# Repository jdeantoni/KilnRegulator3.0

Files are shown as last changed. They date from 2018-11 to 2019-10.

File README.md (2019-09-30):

# KilnRegulator3.0
The objective is to provide a cheap and up to date kiln regulator based on a micro controller and a smart phone app
Please clone with ``git clone --recursive https://github.com/jdeantoni/KilnRegulator3.0.git``

## Website

https://jdeantoni.github.io/KilnRegulator3.0/

## Server readme

See `raspberrypi/`

## Client readme

See `mobile/`

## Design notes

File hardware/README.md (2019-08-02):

this folder contains the electronic level of the kiln regulator, i.e., breakboard, schematics, PCB, etc.
The development is made with Fritzing (https://fritzing.org/home/)

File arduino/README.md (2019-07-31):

# Prepare

Download and extract the Arduino IDE from
https://www.arduino.cc/en/Main/Software

Then set the environment variables according to the path of the extracted Arduino IDE (assuming it is in the current directory):
```
export ARDUINO_DIR="$(pwd)/arduino-1.8.7"
export PATH="${PATH}:${ARDUINO_DIR}"
```

Supported versions: 1.8.3 to 1.8.7 (included)

On ArchLinux, simply install the `arduino` package from the community repository.

# Build

```
git submodule update --init
make
```

# Deploy

```
make upload
```

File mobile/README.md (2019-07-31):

# KilnRegulator Client in React Native

## Dependencies

Install Expo, React Native and the project dependencies:

```
sudo npm install expo-cli --global
sudo npm install react-native-cli --global
npm install
```

## Build

Generate API client from Swagger:

```
./generate-client.sh
```

## Run

Launch the project on your terminal with Expo:

```
expo start
```

For the next steps, follow the instructions on your terminal and your browser at http://localhost:19002/.
If you want to use your own phone to test the app, download the [Expo app](https://expo.io) on your phone and scan the QR code from Expo.
Open it in the [Expo app](https://expo.io) on your phone to view it.

## Notes

In case of errors:
- If there is a connection error, please go to the webpage opened when you launched `expo start`, choose the *tunnel* mode and open it again in the expo app.
- For the emulation, check if `adb` is updated. If you have more than one installations of ADB, check the versions.
If you are using Genymotion, localize the Android SDK in the settings.
- Check if the ip address is correct. You may have to modify it each time you change your network.
With PowerShell:
```
$env:REACT_NATIVE_PACKAGER_HOSTNAME = “<IP>”
```
- If the terminal displays some errors, don't hesitate to reload Expo.
- If the QR code doesn't appear, reload Expo.
- If the bundle can't be constructed, add a dummy line in the code, the build may start.
- Check there is an unique instance of the app on your phone.

## Deploy

### Prepare

Make sure the `ANDROID_HOME` environment variable is set to the Android SDK path, eg. `~/Android/Sdk`:
```
export ANDROID_HOME="$HOME/Android/Sdk"
```

#### Eject

```
./eject.sh
```

#### Generate signing key

```
keytool -genkey -v -keystore android/app/my-release-key.keystore -alias my-key-alias -keyalg RSA -keysize 2048 -validity 10000 -storepass "password" -keypass "password" -dname "CN=Unknown, OU=Unknown, O=Unknown, L=Unknown, ST=Unknown, C=Unknown"
```

#### Add signing configuration

```
patch -p1 -i android-sign.patch
```

### Build & deploy

#### Generate signed apk

```
./android/gradlew -p android assembleRelease
```

#### Install signed apk

```
adb install ./android/app/build/outputs/apk/release/app-release.apk
```

## Screen navigation

### Home Page

When the app is launched, the home page display two buttons:
* You can connect your device to your kiln using the server IP address (don't forget the port).
* If you're not next to your kiln, there is an off line mode.

### Program choice

You can modify and create programs from this page. Select a program in the list, then, you have four options:
* Edit the program
* Duplicate the program
* Delete the program
* Launch the program

### Program edition

Edit the program in this page. You can edit the segments in the table and see results in the graph.
See in precision the temperature evolution with a cursor on the graph.

### Settings

Import and export kiln and phone programs.

### Tracking cooking

See the temperature evolution of the cooking. In brown, you can see the theoretical points, and in green the real ones.
When you connect your device with a kiln already heating, you will see first this screen.
When the kiln is stopped, you will see the last data from the cooking and the button will reinitialize the kiln state.
If an error appear, the icon in the header bar will change and you can access to the errors list.

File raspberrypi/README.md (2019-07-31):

# KilnRegulator Server on RaspberryPi

Arduino code will be automatically built and deployed on the Arduino when running through `docker-compose`.

## Dependencies (to be installed on the Raspberry or the development environment accordingly)
This README considers that the Raspbian OS is already installed on the Raspberry (see https://www.raspberrypi.org/downloads/raspbian/).

```
docker
docker-compose
```

## Prepare

To configure the Raspbian installation with a WiFi access point, watchdog, etc see conf/README.md

The arduino is connected through usb serial to the raspberry and the rasberry connected to the development computer (e.g., by using ethernet). Then, in the later, you can either connect to the raspberry through ssh or directly launch commands on the raspberry. But First, on the raspberry

Edit `raspberrypi/conf/udev/rules.d/arduino.rules` replacing the `idVendor` and `idProduct` by those of your Arduino device (that can be found in dmesg for instance).

```
sudo cp raspberrypi/conf/udev/rules.d/arduino.rules /etc/udev/rules.d
```

On Raspberry Pi:
```
git submodule update --init rpi3-mongodb3
```

## Build
From the root of the project,

```
docker-compose build
```

Or on Raspberry Pi:
```
docker-compose -f docker-compose-rpi.yml build
```

## Run

Arduino container is started before the server for it to deploy the code first then free the serial port for the server.

From the root of the project,

```
docker-compose up arduino && docker-compose up mongo server
```

Or on Raspberry Pi:
```
docker-compose -f docker-compose-rpi.yml up arduino && docker-compose -f docker-compose-rpi.yml up mongo server
```

## Notes

API can be viewed and tried at http://localhost:3000/docs

Bug with Linux 4.19 and Docker 18.09
https://github.com/docker/for-linux/issues/480

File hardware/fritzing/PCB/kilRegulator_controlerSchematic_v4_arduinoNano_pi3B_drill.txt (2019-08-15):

; NON-PLATED HOLES START AT T1
; THROUGH (PLATED) HOLES START AT T100
M48
INCH
T1C0.117717
T2C0.078740
T3C0.106299
T4C0.110236
T100C0.035000
T101C0.042000
T102C0.036000
T103C0.047244
T104C0.039370
T105C0.038000
T106C0.098425
T107C0.015748
%
T1
X024261Y001476
T2
X008839Y021483
X002934Y021483
X008761Y005676
X002961Y005676
T3
X024261Y020676
X001461Y020676
X024361Y008976
T4
X001461Y001376
T100
X011595Y015183
X016829Y020354
X015595Y015183
X021438Y015361
X019214Y014746
X016882Y015361
X021438Y020301
T101
X017894Y012821
X020874Y012821
T102
X002861Y019576
X002861Y010576
X002861Y008576
X008861Y017576
X008861Y020576
X008861Y009576
X002861Y011576
X008861Y019576
X008861Y016576
X008861Y018576
X002861Y006576
X008861Y010576
X008861Y007576
X002861Y009576
X002861Y013576
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

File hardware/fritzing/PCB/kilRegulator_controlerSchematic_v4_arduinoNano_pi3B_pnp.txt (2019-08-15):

*Pick And Place List
*Company=
*Author=
*eMail=
*
*Project=kilRegulator_controlerSchematic_v4_arduinoNano_pi3B
*Date=16:24:04
*CreatedBy=Fritzing 0.9.3b.04.19.5c895d327c44a3114e5fcc9d8260daf0cbb52806
*
*
*Coordinates in mm, always center of component
*Origin 0/0=Lower left corner of PCB
*Rotation in degree (0-360, math. pos.)
*
*No;Value;Package;X;Y;Rotation;Side;Name
1;;;24.4348;-29.4046;0;Bottom;Copper Fill4
2;;;29.0576;-29.5316;0;Bottom;Copper Fill5
3;;;38.4556;-34.4338;0;Bottom;Copper Fill30
4;;;28.2194;-7.0018;0;Bottom;Copper Fill14
5;;;53.37;-13.149;90;Bottom;Max31856
6;;;30.8864;-7.6368;0;Bottom;Copper Fill13
7;;;14.889;-34.4935;180;Bottom;arduino
8;;;33.4712;-15.5907;0;Bottom;Via1
9;;;8.2296;-20.5146;0;Bottom;Copper Fill10
10;;;40.8065;-14.6831;0;Bottom;Via5
11;;;40.8118;-5.77023;0;Bottom;Via4
12;;;40.7797;-6.3414;0;Bottom;Copper Fill36
13;;;58.2676;-21.048;0;Bottom;Copper Fill32
14;;SIP (Single Inline) [THT];22.0357;-3.28432;-90;Bottom;Screen (bottom side)
15;;;11.8237;-4.2332;0;Bottom;Copper Fill17
16;;;48.6446;-45.2714;180;Bottom;relay
17;;;33.2994;-8.3988;0;Bottom;Copper Fill12
18;;;15.8496;-27.8298;0;Bottom;Copper Fill3
19;;;44.2722;-28.7061;0;Bottom;Copper Fill41
20;;;40.7797;-5.3508;0;Bottom;Copper Fill37
21;;;7.523;-14.419;0;Bottom;Hole7
22;;;33.8074;-22.572;0;Bottom;Copper Fill34
23;;;30.7305;-49.3091;0;Bottom;TXT1
24;;;23.2918;-24.3881;0;Bottom;Copper Fill24
25;;;40.2844;-5.8461;0;Bottom;Copper Fill20
26;;;41.2496;-5.8461;0;Bottom;Copper Fill21
27;;;11.8237;-2.4552;0;Bottom;Copper Fill18
28;;;3.713;-52.519;0;Bottom;Hole14
29;;;32.2834;-28.1092;0;Bottom;Copper Fill1
30;;SOT-23 [SMD];43.017;-29.643;0;Top;Q3
31;;;44.2214;-18.2921;0;Bottom;Copper Fill27
32;;;17.3228;-29.557;0;Bottom;Copper Fill2
33;;;30.6422;-51.8527;0;Bottom;TXT1
34;;;3.713;-3.49698;0;Bottom;Hole13
35;;;8.2296;-23.0546;0;Bottom;Copper Fill9
36;;;26.8986;-34.4846;0;Bottom;Copper Fill8
37;;;40.7797;-5.3508;0;Bottom;Copper Fill19
38;;;32.4866;-23.8166;0;Bottom;Copper Fill33
39;;;40.259;-14.7361;0;Bottom;Copper Fill42
40;;;22.8346;-28.1092;0;Bottom;Copper Fill29
41;;;45.8978;-18.2921;0;Bottom;Copper Fill28
42;;;7.453;-54.567;0;Bottom;Hole5
43;;;61.625;-52.519;0;Bottom;Hole11
44;;;8.2296;-17.9746;0;Bottom;Copper Fill11
45;;;27.9146;-27.6266;0;Bottom;Copper Fill7
46;;;41.2496;-14.7361;0;Bottom;Copper Fill43
47;;;22.255;-14.419;0;Bottom;Hole8
48;;;41.2496;-14.7361;0;Bottom;Copper Fill26
49;;;61.625;-3.75098;0;Bottom;Hole10
50;;;6.4262;-19.3081;0;Bottom;Copper Fill22
51;;;41.2496;-5.8461;0;Bottom;Copper Fill38
52;;;14.3637;-4.2332;0;Bottom;Copper Fill15
53;;;32.4309;-54.3536;0;Bottom;TXT1
54;;screwterminal-3.5mm-2_lock;60.709;-47.0352;-90;Bottom;JP1
55;;;61.879;-22.801;0;Bottom;Hole9
56;;;22.453;-54.567;0;Bottom;Hole6
57;;;8.0518;-19.3081;0;Bottom;Copper Fill39
58;;;45.8978;-18.2921;0;Bottom;Copper Fill44
59;;;40.259;-14.7361;0;Bottom;Copper Fill25
60;220;THT;34.5331;-38.567;180;Bottom;R1
61;;;14.3637;-2.4552;0;Bottom;Copper Fill16
62;;300 mil [THT];49.2377;-32.567;180;Bottom;D1
63;;;23.2918;-24.3881;0;Bottom;Copper Fill40
64;;;48.9966;-12.3866;0;Bottom;Copper Fill35
65;;;21.6662;-24.3881;0;Bottom;Copper Fill23

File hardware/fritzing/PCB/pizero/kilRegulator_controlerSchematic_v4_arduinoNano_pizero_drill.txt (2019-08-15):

; NON-PLATED HOLES START AT T1
; THROUGH (PLATED) HOLES START AT T100
M48
INCH
T1C0.078740
T2C0.106299
T3C0.094488
T100C0.035000
T101C0.042000
T102C0.036000
T103C0.047244
T104C0.039370
T105C0.038000
T106C0.098425
T107C0.015748
%
T1
X008839Y021911
X008761Y006105
X002961Y006105
X002934Y021911
T2
X024587Y001833
X024587Y009313
T3
X024461Y011205
X001361Y001805
X001361Y011205
T100
X011595Y015612
X019214Y015174
X015595Y015612
X016882Y015790
X021438Y015790
X016829Y020783
X021438Y020730
T101
X020874Y013250
X017894Y013250
T102
X008861Y019005
X008861Y018005
X002861Y016005
X002861Y009005
X008861Y015005
X008861Y012005
X002861Y008005
X008861Y011005
X002861Y012005
X008861Y020005
X002861Y007005
X002861Y014005
X008861Y013005
X008861Y007005
X002861Y015005
X008861Y009005
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

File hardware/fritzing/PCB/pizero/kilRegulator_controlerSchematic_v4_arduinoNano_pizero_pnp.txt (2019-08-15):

*Pick And Place List
*Company=
*Author=
*eMail=
*
*Project=kilRegulator_controlerSchematic_v4_arduinoNano_pizero
*Date=16:39:52
*CreatedBy=Fritzing 0.9.3b.04.19.5c895d327c44a3114e5fcc9d8260daf0cbb52806
*
*
*Coordinates in mm, always center of component
*Origin 0/0=Lower left corner of PCB
*Rotation in degree (0-360, math. pos.)
*
*No;Value;Package;X;Y;Rotation;Side;Name
1;;;21.6408;-25.4766;0;Bottom;Copper Fill20
2;;;62.1329;-28.4615;0;Bottom;Hole11
3;;SOT-23 [SMD];42.403;-30.6555;0;Top;Q3
4;;;17.3482;-30.2645;0;Bottom;Copper Fill2
5;;;3.45891;-4.58549;0;Bottom;Hole13
6;;;33.4712;-16.6791;0;Bottom;Via1
7;;;48.6445;-46.3599;180;Bottom;relay
8;;;33.2994;-9.1063;0;Bottom;Copper Fill8
9;;;22.4528;-55.6555;0;Bottom;Hole6
10;;;44.45;-33.7062;0;Bottom;Copper Fill18
11;;;41.9862;-31.6742;0;Bottom;Copper Fill31
12;;;26.8986;-35.5731;0;Bottom;Copper Fill7
13;;;11.8237;-4.5597;0;Bottom;Copper Fill13
14;;;42.8117;-39.3323;0;Bottom;Copper Fill15
15;;;33.1891;-55.4421;0;Bottom;TXT1
16;;;29.928;-55.494;0;Bottom;TXT2
17;;;22.255;-15.5074;0;Bottom;Hole8
18;;;62.4528;-4.65562;0;Bottom;Hole10
19;;;14.3637;-2.7817;0;Bottom;Copper Fill12
20;;;28.2194;-7.7093;0;Bottom;Copper Fill10
21;;300 mil [THT];49.2376;-33.6555;180;Bottom;D1
22;;;62.4528;-23.6554;0;Bottom;Hole9
23;;;58.3184;-21.5777;0;Bottom;Copper Fill26
24;;;45.4025;-32.7791;0;Bottom;Copper Fill34
25;;SIP (Single Inline) [THT];22.0356;-3.61069;-90;Bottom;Screen (bottom side)
26;;;8.0518;-20.3966;0;Bottom;Copper Fill33
27;;;31.2922;-52.6523;0;Bottom;TXT1
28;;;23.2664;-25.4766;0;Bottom;Copper Fill21
29;;;46.3296;-33.7062;0;Bottom;Copper Fill35
30;;screwterminal-3.5mm-2_lock;60.963;-48.6317;-90;Bottom;JP1
31;;;29.0576;-30.6201;0;Bottom;Copper Fill4
32;;;24.4094;-30.4931;0;Bottom;Copper Fill3
33;;;32.3342;-28.6389;0;Bottom;Copper Fill1
34;;;32.766;-24.8543;0;Bottom;Copper Fill27
35;;;28.0839;-48.7986;0;Bottom;TXT2
36;220;THT;34.533;-39.6555;180;Bottom;R1
37;;;46.3296;-33.7062;0;Bottom;Copper Fill19
38;;;45.4025;-32.7791;0;Bottom;Copper Fill17
39;;;23.2664;-25.4766;0;Bottom;Copper Fill36
40;;;26.7462;-28.6389;0;Bottom;Copper Fill29
41;;;7.52301;-15.5074;0;Bottom;Hole7
42;;;34.1122;-23.5843;0;Bottom;Copper Fill28
43;;;31.8251;-52.2579;0;Bottom;TXT2
44;;;14.3637;-4.5597;0;Bottom;Copper Fill11
45;;;27.94;-28.7151;0;Bottom;Copper Fill6
46;;;35.0277;-49.6393;0;Bottom;TXT1
47;;;42.7228;-31.6742;0;Bottom;Copper Fill32
48;;;44.8564;-19.2282;0;Bottom;Copper Fill22
49;;;6.4262;-20.3966;0;Bottom;Copper Fill16
50;;;14.8889;-35.582;180;Bottom;arduino
51;;;11.8237;-2.7817;0;Bottom;Copper Fill14
52;;;15.6464;-2.3753;0;Bottom;Copper Fill30
53;;;54.0049;-14.1105;90;Bottom;Max31856
54;;;3.45891;-28.4615;0;Bottom;Hole12
55;;;7.45302;-55.6555;0;Bottom;Hole5
56;;;38.4302;-35.4715;0;Bottom;Copper Fill24
57;;;46.5328;-19.2282;0;Bottom;Copper Fill23
58;;;43.6372;-29.693;0;Bottom;Copper Fill37
59;;;30.8864;-8.3443;0;Bottom;Copper Fill9

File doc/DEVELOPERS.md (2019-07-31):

# Developer's manual

## Overall architecture

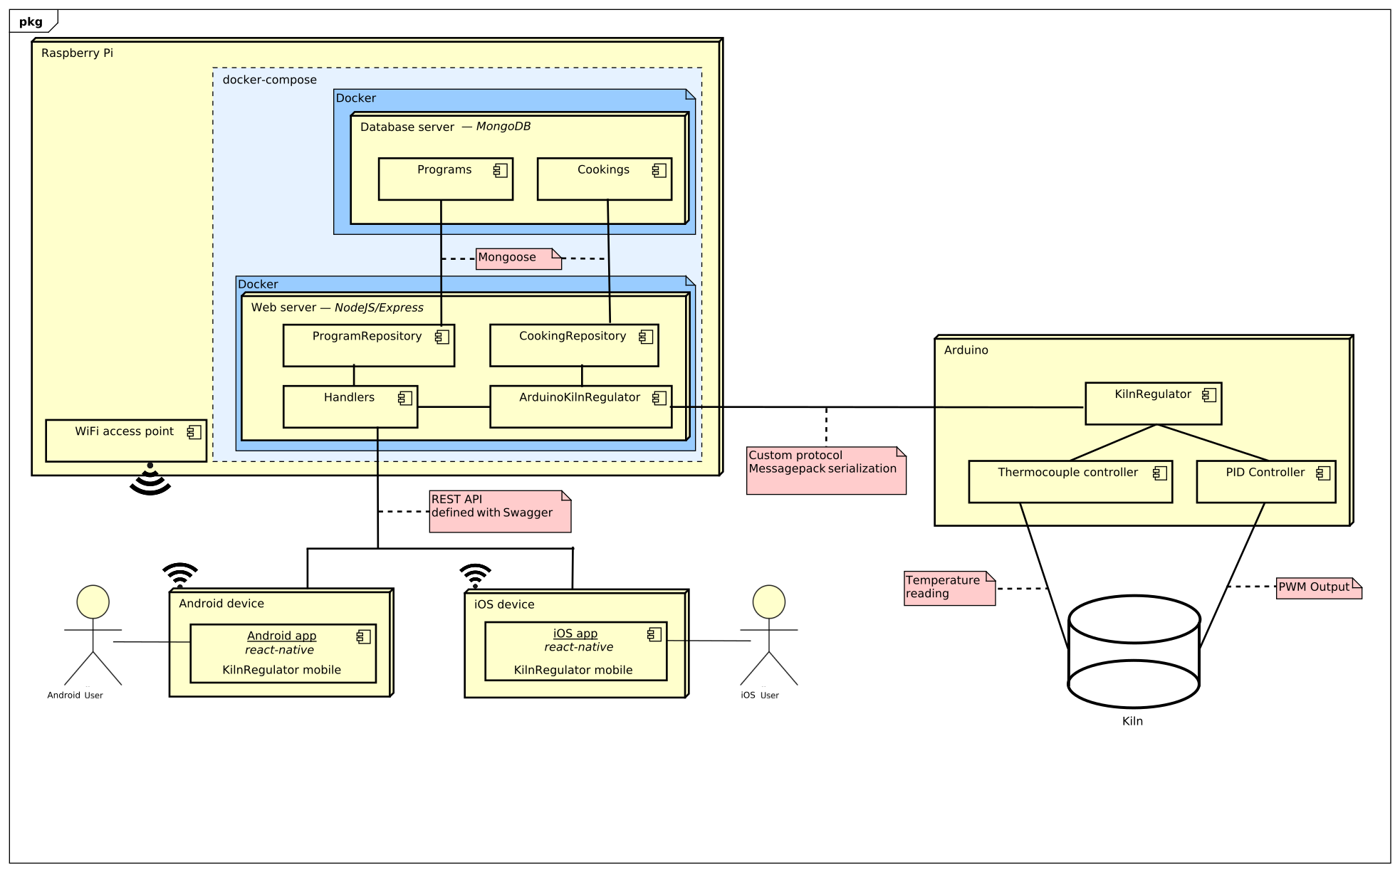
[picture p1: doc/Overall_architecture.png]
Croquis


### Communication protocol between Raspberry Pi Server and Arduino

Communication between the Raspberry Pi and Arduino is done through the virtual serial port exposed on top of the Arduino USB link.

Messages are serialized from JavaScript objects to Messagepack binary format.

Raspberry Pi Server sends command to the Arduino upon request coming from the client trough the REST API.

Commands sent to the Arduino are:
 * `["start", segmentCount]`: start the program transmitted through `segment` commands, switching from "ready" to "running" state
 * `["stop"]`: stop the current program before it has ended, forcing a switch from "running" to "stopped" state
 * `["reset"]`: reset to initial state, switching from "stopped" to "ready" state
 * `["segment", segmentNumber, targetTemperature, slope, duration]`: transmit a segment for the next program to run
 * `["timesync", timestamp]`: send current timestamp (in seconds) to synchronize Arduino's clock
 * `["setpoint", setpoint]`: manually set the target temperature

Arduino regularly sends status update:
```
{
	"command": "status",
	"s": kilnState,
	"eS": elementState,
	"cS": currentSegment,
	"t": temperature,
	"o": output,
	"sP": setPoint,
	"ts": timestamp
}
```
and timesync requests:
```
{
	"command": "timesync"
}
```

Message from the Raspberry Pi Server to the Arduino are always acknowledged by the Arduino. The Arduino compute a CRC8 of the received data and append it to the acknowledgment. Message contains a sequence ID that is sent back in the acknowledgment.

### Raspberry Pi Server REST API for Mobile client

REST API between the Raspberry Pi NodeJS server and the mobile React-Native app is defined using Swagger in the `doc/swagger.yaml` file.

After spinning up the Raspberry Pi NodeJS server (see below), the API documentation can be seen at <http://localhost:3000/docs>. API can be queried from inside the Swagger user interface, or by using the web browser or a command line utility such as `curl` for testing purposes.

The Raspberry Pi NodeJS server parses the Swagger file at runtime to handle routing.

The client libraries must be generated again from a Swagger editor or the command line Swagger generator after modifying the API description.

## Arduino

### Development environment

Arduino development requires installing the Arduino IDE locally. See `arduino/README.md`.
Although it may possibly be working on other platforms, the build system was used only on Linux so far.

#### Development

Please do not use the Arduino IDE itself but rather a standard text editor with EditorConfig support or an IDE with EditorConfig support as well.

#### Build & run

Connect the Arduino on a USB port and use the provided Makefile build system inside the `arduino` folder. Make sure the current user can write to the virtual serial port, check your distribution documentation if needed.

```
cd arduino
make upload
```

### Code style

Defined in `arduino/.editorconfig`
 * Single tab for indendation
 * LF line ending

### Code architecture

All the libraries are added as git submodules under the `src/` folder. Only the `src/kilnregulator/` subfolder actually contains original source code for the Arduino application.

## Raspberry Pi server

### Development environment

Raspberry Pi server development can be done both on a Raspberry Pi 3 or a standard computer with a Linux distribution, although keep in mind that the architecture is different. Raspberry Pi 3 is ARMv7-A (armhf on Debian), a PC is x86_64 (amd64 on Debian, note that i686 is not supported).

Raspberry Pi development requires `nodejs >= 8` and `npm` locally. Make sure you use a recent `npm` version or else modules may fail installing (repository server may throw 405 errors). You may encounter this issue with the latest `npm` package on Raspbian.

#### Development

Use the text editor or IDE of your choice, preferably with EditorConfig support or set the code style parameters manually.

#### Build & run

When running for the first time, start the MongoDB database inside Docker.
```
docker-compose up mongodb
```
Or on Raspberry Pi:
```
docker-compose -f docker-compose-rpi.yml up mongodb
```

Then connect the Arduino (deploy the Arduino code if needed, see above) and start the server:
```
cd raspberrypi
npm start
```

### Code style

Defined in the top-level `.editorconfig`
 * Two spaces for indendation
 * LF line ending

### Code architecture

#### `handlers/`

Request handlers, called by Swagger from the routes defined in the Swagger file. The name of the file must match the `operationId` of the route. A handler must always send something to the client, even an empty string if nothing needs to be sent. Most of the business logic is offloaded to modules inside `services/`

Please read Swagger documentation for details on the purpose of the handlers.

#### `services/`

Business logic for Arduino communication and database objects management.

 * `arduino.js`: encapsulate the Arduino serial port management
 * `arduinomessagepack.js`: manages the Arduino communication protocol: messagepack serialization/deserialization, output buffer, acknowledgments, timeout
 * `arduinokilnregulator.js`: operations on the Arduino as a KilnRegulator module such as handling a state update and stopping/starting a cooking
 * `arduinorepository.js`: Detects and maintain a list of available Arduino (as ArduinoKilnRegulator objects)
 * `cookingrepository.js`: some CRUD operations to manage cookings in database
 * `programrepository.js`: some CRUD operations to manage programs in database
 * `errorhandler.js`: error loggers with 4 severity levels, from warnings, recoverable errors to fatal errors and panic

#### `model/`

Database object models, state machine enums are also declared here, matching the enums declared in Arduino code. Objet models try to match the ones used for the REST API, declared in the Swagger file.

 * `kilnState.js`, `elementState.js`: state machine enums matching Arduino enums, not related to database
 * `db.js`: database connection handler
 * `model.js`: list of database object models
 * `cooking.js`, `program.js`: some object models to store cookings and programs in database

## Mobile app

### Development environment

#### Development

For React Native development, there is no specific IDE to work with, but you can use WebStorm, Visual Studio Code, Atom (with the plugin Nuclide) or your favorite JS text editor.
But you need to have installed on your computer: `npm`, `expo-cli` and `react-native-cli` (npm packages). For more information, see `mobile/README.md`.

#### Build & run

Connect your Android phone or your iPhone on the same network as your computer. Launch the Expo CLI. With the Expo app on your phone, scan the QR code on Expo CLI. Every modification in the code will reload the app on your phone.
```
cd mobile
expo start
```
When the app is opened, connect the mobile to the Raspberry Pi using its IP address (like: 123.1.1.1:3000). Don't forget the port.

### Code style

Defined in `.editorconfig` and modified in `mobile/.editorconfig`
 * Four spaces for indendation
 * LF line ending

### Code architecture

#### At root
 * `app.js`: program entry point (initialize the navigation tool and Redux).
 * `package.json`: list of dependencies.

#### `components/`
Contains all graphic components (table, charts, list items...). This components are reusable in several screens.

#### `screens/`
Represents project pages. Contains the main logic.

#### `navigation/`
Defines the stack navigation. All the screens must be declared here.

#### `helpers/`
Toolbox which contains useful functions. Mainly:
 * `ImageLoader.js`: Registers pictures and icons contained in the `assets/` directory.
 * `NavigationHelper.js`: Helps to edit the header bar.
 * `UnitsHelper.js`: Manages all units conversions (temperature, slope, time...).

#### `network/`
Used to call KilnRegulator3.0 API.
 * `APIClient.js`: Defines the differents client objects for each Swagger tag.
 * `NetworkRoutes`: Memorizes the server IP address.
 * `jsclient/`: Code generated by Swagger to call the API. Don't forget to generate it with the `mobile/generate-client.sh` script.

#### `store/`
Redux files needed to save programs with segments in a global local state. Use actions defined in `helpers/Constants.js` to alter the programs.

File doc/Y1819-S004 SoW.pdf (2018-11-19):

CASAGRANDE Guillaume, NOVAC Pierre-Emmanuel

# KilnRegulator3.0 (Y1819-S004)

## Introduction

Ce projet a pour but d’aider les céramistes dans le processus de cuisson. Notre rôle sera de proposer un système capable de contrôler une cuisson en se greffant aux fours de potiers. Ce genre de système existe déjà mais coûte plusieurs centaines voire milliers d’euros selon les modèles. Proposer un produit bien moins cher est donc l’une de nos priorités.

Les systèmes déjà existants sont fiables mais proposent peu de fonctionnalités. Les possibilités de personnalisation de cuisson étant réduites, nous souhaitons les élargir en proposant une application mobile permettant de créer et de modifier des programmes de cuisson précis. Cette application aura aussi pour but de suivre l’évolution des cuissons au cours du temps.

Cependant, pour convaincre les céramistes, il faudra proposer un système facile à prendre en main ressemblant aux produits qu’ils ont l’habitude de manipuler. Finalement, notre problématique est d’arriver à concevoir un système simple contrôlant une cuisson de poterie, moins coûteux que les produits existants sur le marché et proposant de nouvelles fonctionnalités facilitant le travail des céramistes.

## Description de la solution

Pour répondre à la problématique développée précédemment, nous proposerons deux modules qui communiqueront ensemble : une application mobile et un système embarqué (voir Fig. 1).

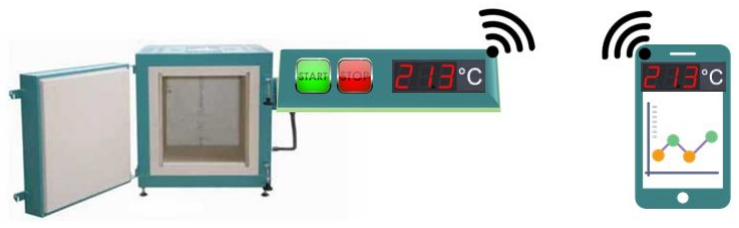
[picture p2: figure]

Figure 1 : Schéma représentatif des éléments majeurs intervenant dans le projet

Personas :
- Ludovic, 36 ans, est potier depuis que son père lui a légué son atelier. En plus de son lieu de travail, son père lui a laissé son savoir faire et une extrême minutie pour son travail. Ludovic aime donc contrôler avec précision le processus de création de ses œuvres. Il utilise un nouveau four qui lui a coûté cher, mais qui lui permet d’obtenir une fiabilité très élevée. Fan de technologie, il aimerait utiliser son téléphone pour contrôler son four, tout en gardant la fiabilité qu’il estime plus que nécessaire. Il souhaite aussi que le système agisse automatiquement ou au moins l’avertisse lors d’une anomalie (par exemple, lors d’une coupure de courant).
- Amélie, 56 ans, céramiste depuis son plus jeune âge, maîtrise largement son domaine. Son atelier fonctionne très bien, surtout grâce aux prix qui battent la concurrence. En fait, Amélie fait ce travail par passion et l’argent ne l’intéresse pas plus que ça. Par contre, son matériel coûte très cher, et elle n’ose pas le remplacer de peur qu’elle soit obligée d’augmenter ses prix. Elle aurait donc besoin d’un système de gestion de cuisson pas cher, voire même réutilisable pour ses différents fours.
- Albert, 44 ans, est un artisan touche-à-tout. Il travaille avec une petite équipe pour fabriquer de nombreux types d’objets en manipulant plusieurs matériaux. Il vend ses œuvres aux marché de sa ville ou à des particuliers sur Internet. Albert est expérimenté dans la céramique, mais cela lui arrive de faire des erreurs. Il oublie souvent qu’il a lancé une cuisson, et ne vérifie pas assez son état. Il aimerait donc un outil afin de suivre l’évolution de sa cuisson quand il est occupé ailleurs.

## Application mobile

### Scénarios d’usage

Scénario 1 :
1) Lancer l’application
2) Connecter l’application au four
3) Choisir le programme numéro 3 correspondant à la porcelaine
4) Démarrer la cuisson
5) Après 3 heures de cuisson, vérifier la température actuelle du four
6) Être alerté de la fin de cuisson

Scénario 2 :
1) Lancer l’application
2) Connecter l’application au four
3) Créer un nouveau programme
4) Identifier les segments du programme
5) Enregistrer le programme
6) Démarrer le programme créé
7) Après 2 heures de cuisson, être alerté qu’un problème est survenu
8) Stopper la cuisson
9) Consulter l’évolution de la température pour identifier le problème

Scénario 3 :
1) Réaliser une cuisson avec de la faïence
2) Trois semaines plus tard, consulter l’historique des cuissons passées
3) Identifier la cuisson de la faïence réalisée précédemment
4) Mémoriser le programme utilisé
5) Modifier le programme en augmentant la température d’un segment de 10°C
6) Démarrer une cuisson avec le nouveau programme

### Maquettes

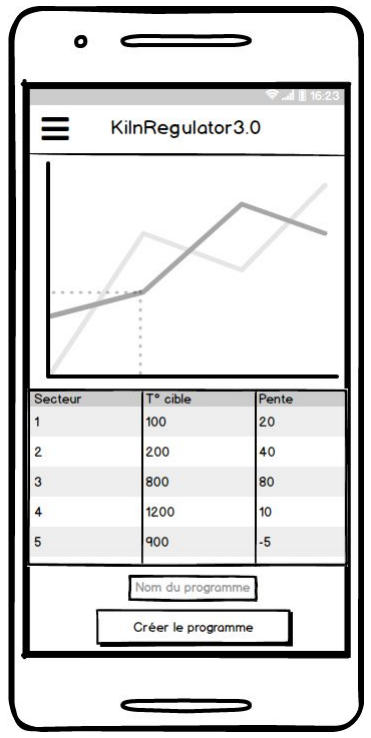
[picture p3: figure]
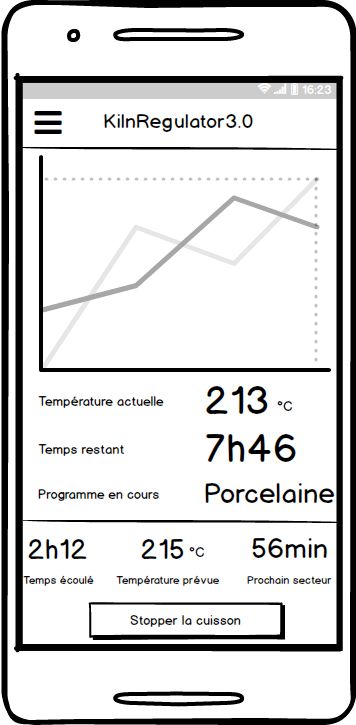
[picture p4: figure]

Figures 2 & 3 : Maquettes du suivi de la cuisson et de la création d’un programme

## Plateforme embarquée

L’application mobile agit sur une plateforme embarquée reliée au four. Cette plateforme doit d’une part assurer le contrôle de la température en suivant du mieux que possible la courbe de température désirée, et d’autre part communiquer avec l’application mobile pour recevoir les commandes et envoyer les données de la cuisson courante. Elle se doit d’être fiable et de prévenir au mieux les incidents ainsi que réagir de manière appropriée lorsqu’ils surviennent.

Pour des raisons de facilité du prototypage, nos choix matériel se concentrent sur des plateformes type Arduino et Raspberry Pi ainsi que des capteurs/actionneurs qui peuvent s’interfacer facilement avec ceux-ci. Plusieurs solutions ont été étudiées comme l’utilisation d’une plateforme Arduino Uno seule, Arduino Mega seule, Raspberry Pi seule ou Raspberry Pi et Arduino Uno, en comparant le prix, les contraintes de chacune et les fonctionnalités offertes. La dernière solution est retenue puisque d’une part elle répond le mieux aux contraintes imposées (robustesse, fiabilité associées à un faible coût) et que d’autre part, elle propose le plus de flexibilité pour l’implantation des fonctionnalités. Dans ce système, l’Arduino s’occupe de la régulation de température et de la gestion des incidents tandis que la Raspberry Pi s’occupe de la communication et de l’enregistrement des données.

### Liste du matériel

Ci-dessous la composition de la plateforme matérielle dans un premier temps :

Qt | Nom | Prix unitaire (€ TTC) | Coût total (€ TTC)
1 | Arduino Uno | 19,50 | 19,50
1 | Raspberry Pi 3 B | 40,00 | 40,00
1 | Carte SD 8 GB | 9,00 | 9,00
1 | Alimentation secteur 5V 3A | 12,00 | 12,00
1 | Module MAX13855 | 7,80 | 7,80
1 | Relai basse tension | 3,00 | 3,00
1 | Afficheur HD44780 | 5,50 | 5,50
3 | Bouton poussoir | 0,30 | 0,90
1 0 | Câble Dupont | 0,20 | 2,00
1 | Optocoupleur (ex. IL250) | 2,00 | 2,00
| Total | | 101,70

Ces composants ont été choisis en particulier pour leur popularité et donc la facilité à se les procurer et à travailler avec. La carte Raspberry Pi 3 pourra être remplacée par exemple par une Raspberry Pi Zero W (23 €) ou une Orange Pi Zero (15 €) pour réduire les coûts. De même, l’Arduino Uno pourra être remplacé par une plateforme équivalente à un coût plus faible.
L’afficheur LCD pourra être remplacé par un écran 128x128 pour afficher la courbe de température par la suite. Les boutons poussoirs pourront servir à sélectionner/démarrer/arrêter un programme directement depuis le four sans passer par l’application.
Il reste à prévoir un boitier pour l’intégration, l’impression 3D pourra convenir pour du prototypage mais pas pour le produit à intégrer sur le four, un boîtier robuste et plus résistant au hautes températures sera nécessaire.
Une maquette mettant en œuvre une Raspberry Pi 3, un Arduino Uno, un thermocouple et son module MAX6675, un élément chauffant et un module de contrôle triac+optocoupleur est visible en annexe 1.

### Contrôle de température

Le contrôle de température se fait en boucle fermée grâce au principe du contrôleur PID. Les coefficients appliqués à chacun des paramètres affecteront les performances du contrôleur, et sont à déterminer expérimentalement. Étant donné que chaque four aura ses propres caractéristiques, une phase de calibration est nécessaire.
L’Arduino mesure en continu la température à l’aide du thermocouple (par l’intermédiaire du convertisseur MAX13855) et détermine la correction à appliquer.

L’Arduino actionne un premier relai de faible puissance, qui agit alors sur un second relai de forte puissance permettant le passage du courant dans la résistance afin d’augmenter la température du four. Réciproquement, le relai est actionné pour bloquer le passage du courant afin de diminuer la température du four, en fonction de la correction à appliquer. L’Arduino contrôle que l’action a bien été effectuée grâce à l’optocoupleur qui mesure un changement d’état (il doit prendre en compte que le courant est alternatif). La connectique présente sur le four propose peut être déjà un moyen de vérifier l’état de la résistance.

### Gestion des incidents

Les incidents suivants sont à gérer avec différents niveaux de criticités et tentative de récupération :
- Valeurs incohérentes récurrentes en provenance du thermocouple : défaut du thermocouple ou du convertisseur
- Dérive trop importante entre température cible et température actuelle : profil incohérent, défaut de l’élément chauffant ou de son contrôle
- Courant circulant dans l’élément chauffant lorsqu’il ne devrait pas chauffer (détecté par l’optocoupleur) : défaut du contrôle de l’élément chauffant
- Courant ne circulant pas dans l’élément chauffant lorsqu’il devrait chauffer (détecté par l’optocoupleur) : défaut de l’élément chauffant ou de son contrôle
- La Raspberry Pi ne reçoit pas de réponse ou reçoit des données corrompues de l’Arduino : défaut de l’Arduino ou du lien de communication
- L’Arduino ne reçoit pas de réponse ou reçoit des données corrompues de la Raspberry Pi : défaut de la Raspberry Pi ou du lien de communication
- Panne de courant
- Arrêt d’urgence (distant ou local)

### Communication

Raspberry Pi/Arduino

Connexion USB classique avec port série virtuel, le protocole de communication devra assurer un minimum d’intégrité des données. On pourra utiliser un protocole de plus haut niveau comme MessagePack et ajouter des sommes de contrôle par exemple après réception du profil de température, et des messages de notification de bonne réception (s’assurer que la commande d’arrêt a bien été transmise par exemple).

Raspberry Pi/Application mobile

Dans un premier temps, la Raspberry Pi fera office de point d’accès WiFi pour permettre une connexion directe du terminal mobile. Les communications se feront à l’aide d’une API REST avec un serveur NodeJS hébergé sur la Raspberry Pi.
Dans un second temps, la Raspberry Pi pourra être configurée pour se connecter à un point d’accès WiFi existant.
Enfin, il est envisageable d’ajouter la prise en charge du Bluetooth, avec côté client et côté serveur une passerelle pour réutiliser l’API REST existante.

## Planning

Prototype 1 – semaine 1 :
- Lancer un programme prédéfini (programme déjà chargé)
- Connecter l’application au boîtier

- Lancer une cuisson depuis l’application (start / stop)
- Réguler en boucle fermée la température
- Afficher la température sur l’application
- Gérer les erreurs critiques
Prototype 2 — semaine 2 :
- Configurer le programme
- Réceptionner le programme
- Enregistrer le programme Prototype 3 — semaine 3 :
- Afficher le suivi de la cuisson
- Récupérer les erreurs non critiques
- Gérer les erreurs
- Alerter en cas de problème Prototype 4 — semaine 3 et 4 :
- Choisir un programme
- Afficher un programme
- Modifier un programme
- Importer / exporter / dupliquer un programme
- Afficher la température et les erreurs sur un écran 7 segments Prototype 5 — semaine 4 :
- Enregistrer les suivis des cuissons
- Afficher le déroulement d’une cuisson
- Afficher l’historique des cuissons Prototype 6 :
- Importer / exporter un historique
- Annoter des programmes
- Annoter des historiques de cuisson
- Envoyer une notification en cas d’erreur
- Envoyer une notification en fin de cuisson
- Consulter à distance l’état de la cuisson

## Conclusion

Après avoir discuté avec des céramistes, nous nous rendons compte à quel point notre outil pourrait faciliter leur quotidien. Cela nous motive pour la suite. Selon le planning que nous avons établi, nous sommes confiants quant à la faisabilité du projet, que ce soit du point de vue embarqué ou mobile.
Nous ne pouvons pas accéder à toutes les demandes des céramistes pour la durée qui nous est accordée. Si le projet a pour vocation de continuer, nous avons d’autres fonctionnalités à proposer. Nous pourrions mettre en place un système d’échanges et de partage de cuissons et de conseils. Nous souhaiterions apporter un système très demandé par les céramistes permettant de fermer le bouchon automatiquement après une durée fixée. Enfin, nous aimerions ajouter du machine learning à notre système afin qu’il puisse conseiller ses utilisateurs quant à la cuisson à programmer.

## Annexes

Annexe 1

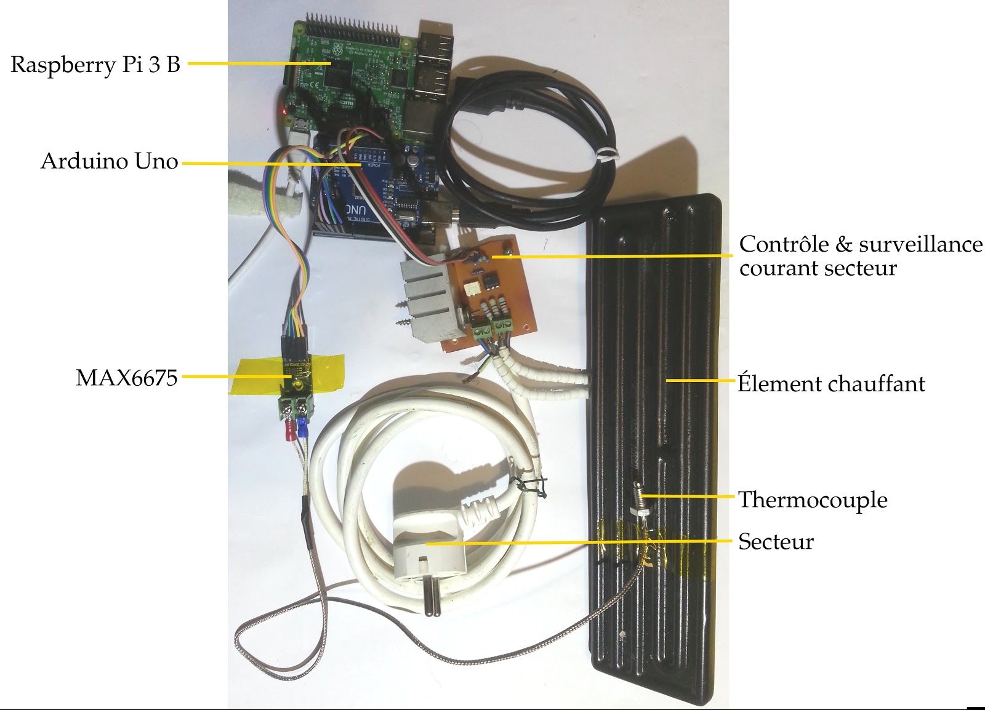
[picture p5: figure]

Figures 4 : Maquette de la plateforme embarquée de contrôle de température

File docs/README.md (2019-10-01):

# KilnRegulator3.0: enfin un application téléphone pour son four

### Vous en avez marre d'acheter des régulateurs de four tout droit sortit des années 80 à un prix exhorbitant ? 
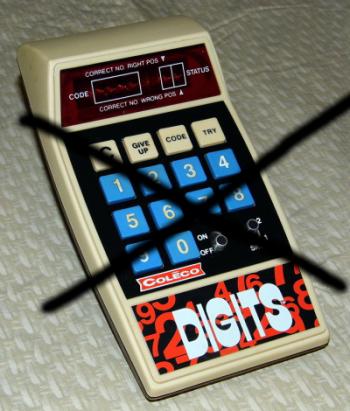
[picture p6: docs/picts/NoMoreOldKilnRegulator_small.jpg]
"les régulateurs actuels !"

### Vous avez envie de pouvoir suivre votre cuisson en temps réel ?
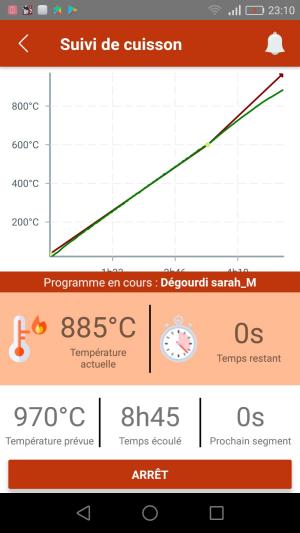
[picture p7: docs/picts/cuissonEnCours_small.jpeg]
"cuisson en cours !"

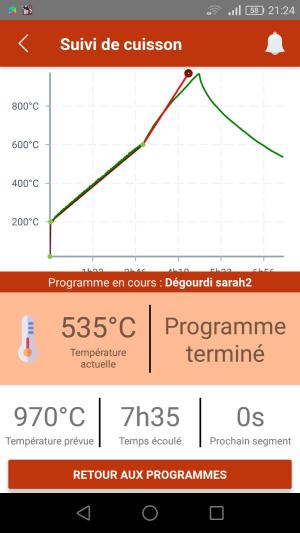
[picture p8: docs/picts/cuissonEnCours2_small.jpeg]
"cuisson en cours2 !"

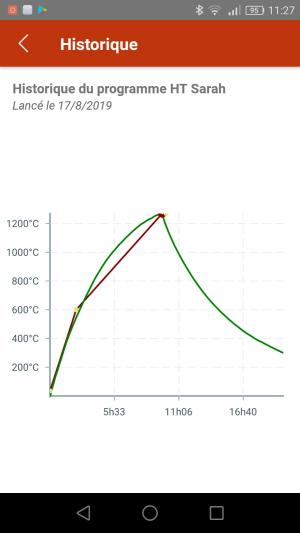
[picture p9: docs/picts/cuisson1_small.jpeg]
"cuisson en cours3 !"

### Vous voulez programmer votre cuisson depuis une interface conviviale ?
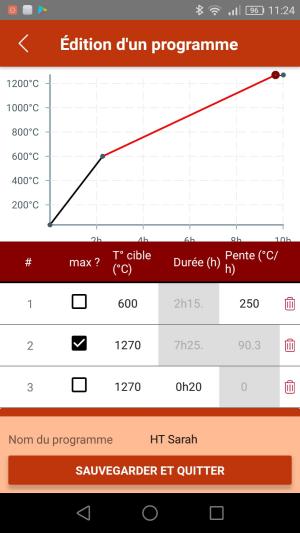
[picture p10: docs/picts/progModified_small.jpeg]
"programmation intuitive !"


### c'est possible grâce au projet [open source KilnRegulator3.0](https://github.com/jdeantoni/KilnRegulator3.0)

Ce projet a été initié par Julien Deantoni et deux ingénieurs (étudiants à l'époque): Guillaume Casagrande et Pierre Emmanuel Novac.
L'idée de départ est de mettre au gout du jour les technologies obsolètes utilisées par la majorité des vendeurs de programmateurs de fours céramiques.

Nous proposons donc un régulateur qui se branche sur les prises classiques des fours de type ceradel ou solargil et qui communique avec une application smartphone (android ou ios) permettant de programmer le four et de voir le suivi de cuisson; le tout pour un prix de revient autour de 70€ environ (et quelques heures de travail) si vous fabriquez tout vous même.

### Une video explicatif du projet initial se trouve [ici](https://youtu.be/vaViCxbbG_A)
<iframe width="560" height="315" src="https://www.youtube.com/embed/vaViCxbbG_A" frameborder="0" allow="autoplay; encrypted-media" allowfullscreen></iframe>

**Notez que le boîtier à bien évolué depuis ;)**:

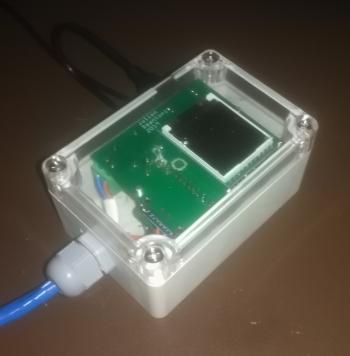
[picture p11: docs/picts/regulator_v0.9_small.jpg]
"le régulateur"


Envie d'en savoir plus ? Contactez moi: julien  _._  deantoni   \at/   gmail   _._    com

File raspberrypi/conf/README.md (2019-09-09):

# KilnRegulator Server on RaspberryPi

## Setup

Raspbian Lite
(note: on pi zero w, to connect through USB do ```touch ssh``` in the boot partition, then append ```dtoverlay=dwc2``` at the end of config.txt and append ```modules-load=dwc2,g_ether``` after rootwait of the line in cmdline.txt)

### Auto

```
cd scripts
./install.sh
```

### Manual

```
sudo apt install hostapd
sudo systemctl disable NetworkManager-wait-online.service
sudo systemctl enable systemd-networkd.service
sudo systemctl enable systemd-resolved.service
sudo systemctl enable avahi-daemon.service

# Network configuration
## DNS using systemd-resolved
sudo rm /etc/resolv.conf
sudo ln -s /run/systemd/resolve/resolv.conf /etc/resolv.conf
## WiFi access point
sudo cp hostapd/hostapd.conf /etc/hostapd/
sudo cp systemd/system/hostapd.service /etc/systemd/system/
sudo systemctl enable hostapd
sudo cp systemd/network/wlan0.network /etc/systemd/network/
## Ethernet
sudo cp systemd/network/eth0.network /etc/systemd/network/
## Bridge
sudo cp systemd/network/br0.netdev /etc/systemd/network/
sudo cp systemd/network/br0.network /etc/systemd/network/
## Wait for network configuration to be up, ignoring wlan0 interface (configured later in the boot process by hostapd)
sudo mkdir /etc/systemd/system/systemd-networkd-wait-online.service.d
sudo cp systemd/system/systemd-networkd-wait-online.service.d/override.conf /etc/systemd/system/systemd-networkd-wait-online.service.d/
sudo systemctl enable systemd-networkd-wait-online.service

# SSH avahi service
sudo cp  /usr/share/doc/avahi-daemon/examples/ssh.service /etc/avahi/services
# KilnRegulator Avahi service
sudo cp avahi/services/kilnregulator.service /etc/avahi/services

#Docker
curl -fsSL https://download.docker.com/linux/debian/gpg | sudo apt-key add -
 echo "deb [arch=armhf] https://download.docker.com/linux/debian \
     $(lsb_release -cs) stable" | \
    sudo tee /etc/apt/sources.list.d/docker.list
sudo apt update
sudo apt-get install docker-ce docker-compose --no-install-recommends
sudo usermod -G docker -a pi

#Watchdog
sudo apt install watchdog
echo -e "# activating the hardware watchdog\ndtparam=watchdog=on" |sudo tee -a /boot/config.txt
cat <<EOF | sudo tee -a /etc/watchdog.conf
# rpi watchdog device
watchdog-device = /dev/watchdog
# rpi watchdog max timeout
watchdog-timeout=15
# some parameters to trigger watchdog on resource exhausted
max-load-1 = 24
min-memory = 8
EOF

# We don't need no swapfile
sudo systemctl disable dphys-swapfile.service
sudo rm -f /var/swap
```

Reboot Raspberry Pi.

## Default settings

| Parameter | Default value | Configuration file |
| --- | --- | --- |
| SSID | KilnRegulator | /etc/hostapd/hostapd.conf |
| Passphrase | KilnRegulator3.0 | /etc/hostapd/hostapd.conf |
| WiFi IP Address | 192.168.1.1 | /etc/systemd/network/wlan0.network |
| Ethernet IP Address | DHCP configured  | /etc/systemd/network/br0.network |

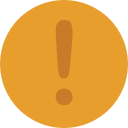
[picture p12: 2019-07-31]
raspberrypi/webSite/html5/assets/picts/warning.png

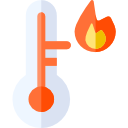
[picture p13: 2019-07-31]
raspberrypi/webSite/html5/assets/picts/heating.png

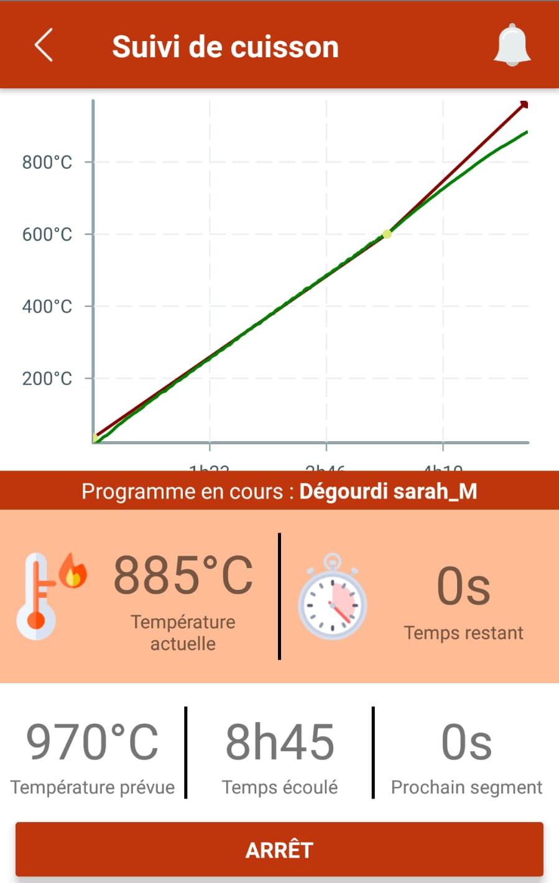
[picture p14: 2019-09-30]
docs/picts/cuissonEnCours.jpeg

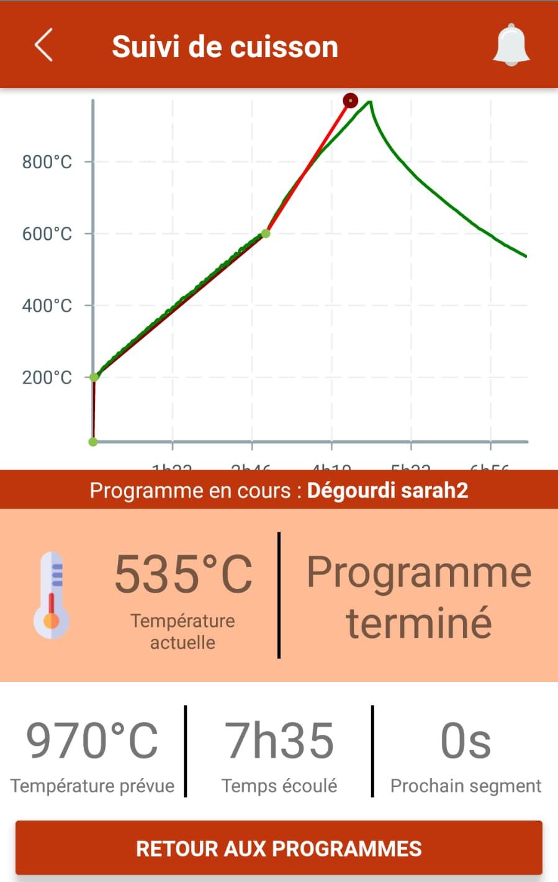
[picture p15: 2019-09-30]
docs/picts/cuissonEnCours2.jpeg

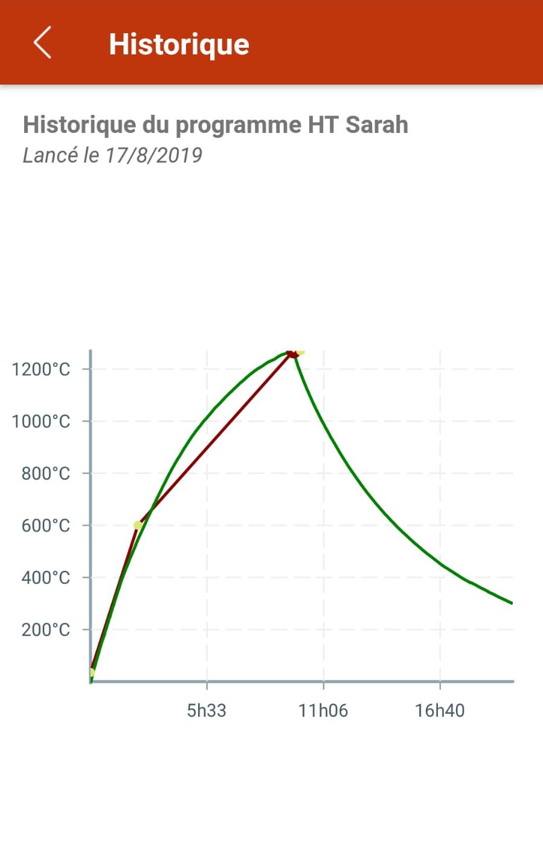
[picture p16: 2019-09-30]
docs/picts/cuisson1.jpeg

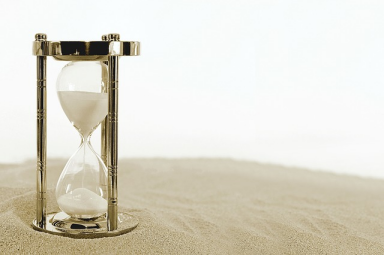
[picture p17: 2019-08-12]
raspberrypi/webSite/html5/assets/picts/sablier.png

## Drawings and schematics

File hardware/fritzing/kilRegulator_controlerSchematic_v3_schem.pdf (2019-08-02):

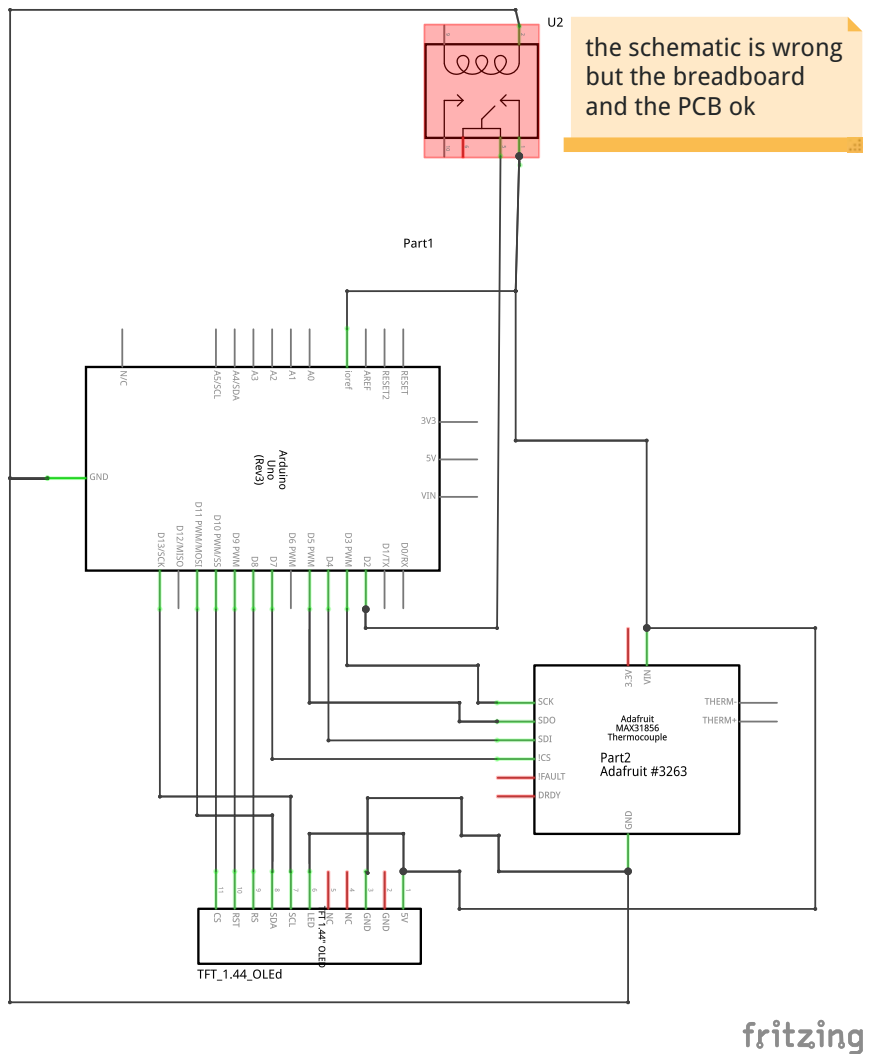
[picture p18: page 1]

the schematic is wrong
but the breadboard
and the PCB ok

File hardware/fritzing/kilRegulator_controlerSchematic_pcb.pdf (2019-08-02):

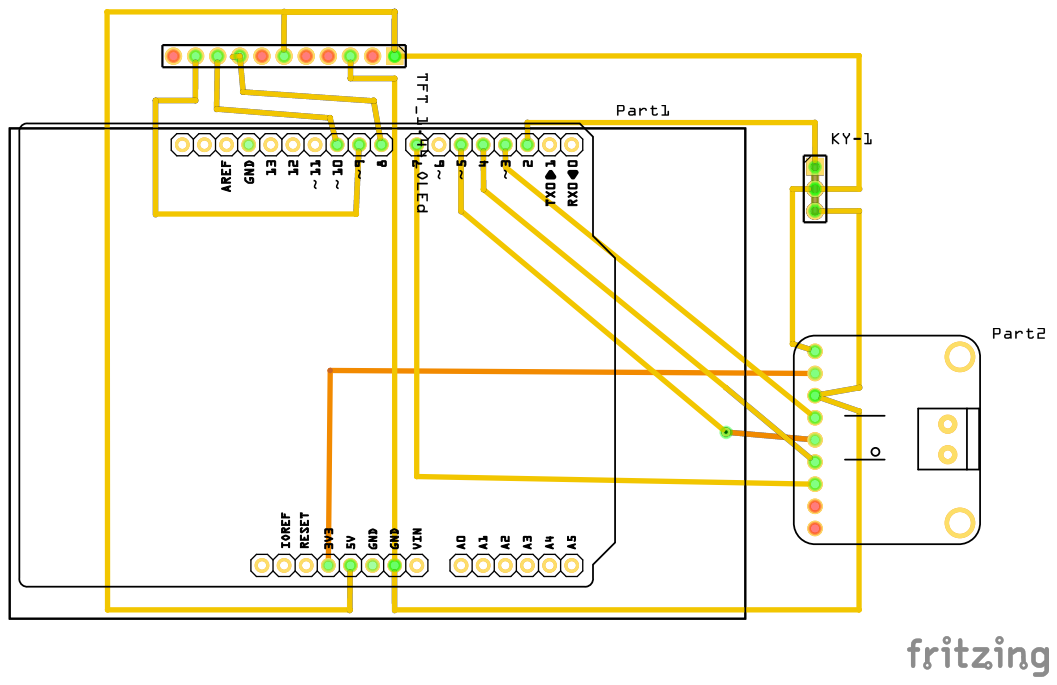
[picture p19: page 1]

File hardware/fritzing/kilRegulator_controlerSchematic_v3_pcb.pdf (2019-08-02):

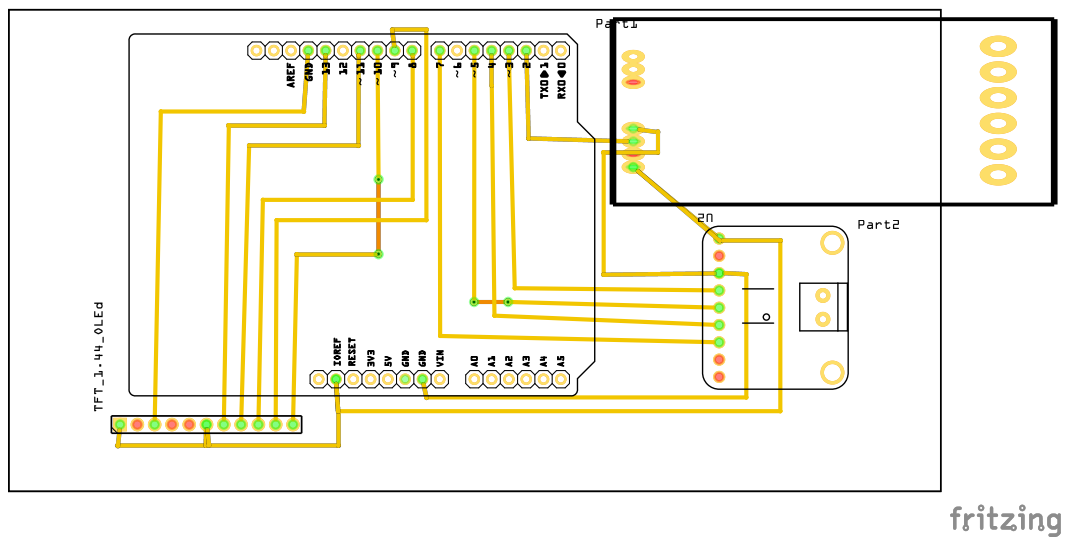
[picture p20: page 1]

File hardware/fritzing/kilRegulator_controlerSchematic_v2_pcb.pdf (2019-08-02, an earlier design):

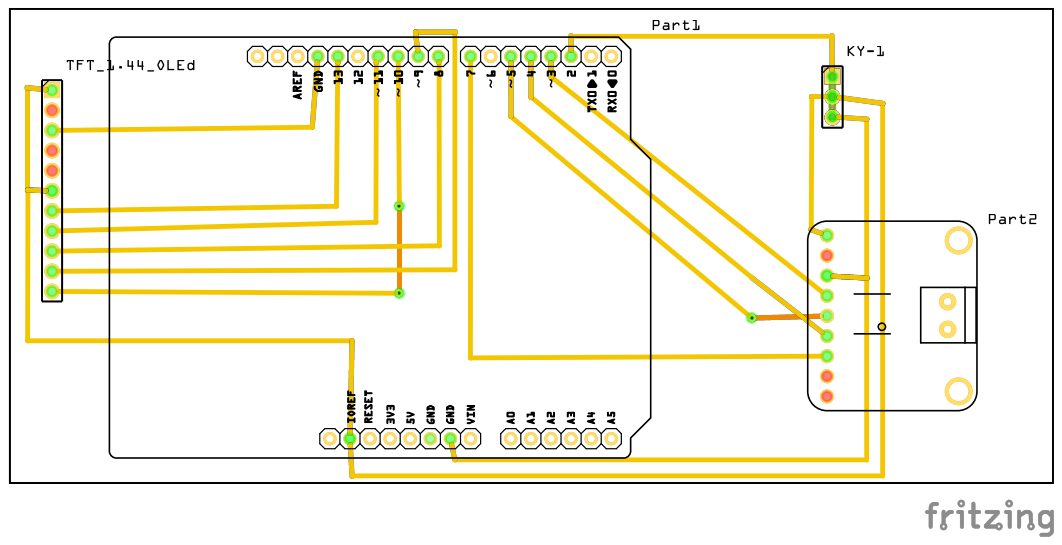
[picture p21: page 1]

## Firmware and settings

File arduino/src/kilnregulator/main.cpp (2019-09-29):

/*
 * Warning: this code relies on millis which will overflow after 50 days.
 * No garantuee are made about this code working when millis overflows
 * Absolute timestamp is in seconds, 32-bit unsigned int. Should overflow after year 2106
 */

#include <msgpack.hpp>
#include <util/crc16.h>

#include <Time.h>
#include <IEEE754tools.h>

#include "KilnRegulator.h"
#include "Segment.h"
#include "Program.h"
#include "StreamCRC.h"
#include "Timer.h"
#include "Time.h"
#include "WatchDog.h"
#include "LCDMonitor.h"

void sendState(Stream &stream, KilnRegulator &kilnRegulator);


#define MAX_KEY_LENGTH 31

////   Adafruit_MAX31856 maxDAC(MAXcs, MAXdi, MAXdo, MAXclk);
Adafruit_MAX31856 thermocouple(/*thermoCS*/7,4,5,3);

KilnRegulator kilnRegulator(thermocouple, /*outputPin*/2);

StreamCRC streamCRC(Serial);

Program program;

Timer samplingTimer{15000}; // 15'000ms sampling rate, more or less…

WatchDog watchdog;

LCDMonitor lcdMonitor(/*cs*/10, /*dc*/8, /*rst*/9);

char key[MAX_KEY_LENGTH+1] = "\0"; // buffer to store received map key

time_t lastTimesyncRequest = 0;
int timeout = 50000;
int timeoutCounter = 0;

// Acknowledgment or error if code != 0
void sendAck(StreamCRC &stream, unsigned long msgId, char action[], int code) {
	size_t mapSize = 4;
	msgpack::writeMapSize(stream, mapSize);

	msgpack::writeString(stream, "ack");
	msgpack::writeString(stream, key);

	msgpack::writeString(stream, "id");
	msgpack::writeIntU32(stream, msgId);

	msgpack::writeString(stream, "code");
	msgpack::writeInt16(stream, code);

	msgpack::writeString(stream, "crc");
	msgpack::writeIntU8(stream, stream.getCRC());
}

time_t requestTime() {
	size_t mapSize = 1;
	if (lastTimesyncRequest > 0) // request already pending, don't try again before timeout
		return 0;
	lastTimesyncRequest = millis();

	msgpack::writeMapSize(streamCRC, mapSize);

	msgpack::writeString(streamCRC, "command");
	msgpack::writeString(streamCRC, "timesync");

	return 0; // the time will be sent later in response to serial msg
}

// just because the encoding process on the NodeJS side will encore a decimal number into an integer if it's dividable by 1
bool forceReadDouble(StreamCRC &stream, double &value) {
	msgpack::DataType dataFormat;
	msgpack::getNextDataType(stream, dataFormat, true);

	if (dataFormat == msgpack::Float64) { // NodeJS sends 64-bit float, we don't support double precision, try it anyway…
		uint64_t v;
		bool e = msgpack::readIntU64(stream, v, false); // read it in a uint64_t which is 8 bytes long, same as the received double, bypassing check since it's not the correct type
		value = doublePacked2Float(reinterpret_cast<unsigned char*>(&v)); // decode the 8bytes "buffer" to a 32bit float
		return e;
	} else if (dataFormat == msgpack::Float32) {
		float v;
		bool e = msgpack::readFloat32(stream, v);
		value = v;
		return e;
	} else { // assume it's an Integer. Bad assumption but who cares at this point
		int v;
		bool e = msgpack::readInt(stream, v);
		value = v;
		return e;
	}
}

/*
 * Message format:
 * [ "command", param]
 *
 * TODO: handle errCode from msgpack functions properly
 */
bool receiveMessage(StreamCRC &stream, KilnRegulator &kilnRegulator) {
	size_t arraySize;
	size_t keyLength;
	int errCode = 0;
	unsigned long msgId = -1;


	/*
	 * CRC computation
	 */
	stream.resetCRC();
	strcpy(key, "request");

	errCode = msgpack::readArraySize(stream, arraySize);
	if (!errCode) { // not error code but success
		errCode = ErrorCode::BAD_REQUEST +10;
		goto readerror;
	}

	if (arraySize < 2 || arraySize > 3) {
		errCode = ErrorCode::BAD_REQUEST +20;
		goto readerror;
	}

	/*
	 * Read message Id
	 */
	errCode = msgpack::readInt(stream, msgId);

	/*
	 * Read command
	 */
	errCode = msgpack::readString(stream, key, sizeof(key), keyLength);
	if (!errCode) { // not error code but success
		errCode = ErrorCode::BAD_REQUEST +30;
		goto readerror;
	}

	if (!strncmp(key, "segment", keyLength+1)) {
		int id = -1;
		double temperature = -1;
		double slope = -1;
		unsigned long duration = 0;
		bool isFull = false;
		errCode = msgpack::readArraySize(stream, arraySize);
		//assert arraySize == 4

		errCode = msgpack::readInt(stream, id);
		errCode = forceReadDouble(stream, temperature);
		errCode = forceReadDouble(stream, slope);
		errCode = msgpack::readInt(stream, duration);
		errCode = msgpack::readBool(stream, isFull);

		//assert id >= 0 && id < MAX_SEGMENT_COUNT

		program.segments[id] = {
			.temperature = temperature,
			.slope = slope,
			.duration = duration,
			.isFull = isFull
		};
		program.count++;
	}

	else if (!strncmp(key, "start", keyLength+1)) { //keyLength+1 because we want to compare null character as well
		//start cooking
		//read program

		// number of segments in the program
		int v = 0;
		errCode = msgpack::readInt(stream, v);
		//assert v == program.count

		errCode = kilnRegulator.start(program);
	} else if (!strncmp(key, "stop", keyLength+1)) {
		errCode = kilnRegulator.stop();
		//stop cooking
	} else if (!strncmp(key, "reset", keyLength+1)) {
		errCode = kilnRegulator.reset();
		program.count = 0;
		//reset cooking
	} else if (!strncmp(key, "timesync", keyLength+1)) {
		if (kilnRegulator.getState() == KilnState::LOADING){
			kilnRegulator.setState(KilnState::READY);
		}
		if (arraySize < 2) {
			errCode = ErrorCode::BAD_REQUEST;
			goto readerror;
		}

		//time synchronisation
		unsigned long timestamp = -1;
		errCode = msgpack::readInt(stream, timestamp);
		if (errCode) { // not error code but success
			setTime(timestamp);
			lastTimesyncRequest = 0;
			timeoutCounter = 0;
		} else {
			errCode = ErrorCode::BAD_REQUEST;
			goto readerror;
		}
	} else if (!strncmp(key, "setpoint", keyLength+1)) { //is it really used ? f so, why ?
		if (arraySize < 2) {
			errCode = ErrorCode::BAD_REQUEST;
			goto readerror;
		}

		long setpoint = -1;
		errCode = msgpack::readInt(stream, setpoint);
		if (errCode) { // not error code but success
			errCode = kilnRegulator.setSetpoint(setpoint);
		} else {
			errCode = ErrorCode::BAD_REQUEST;
			goto readerror;
		}
		//set setpoint
	} else if (!strncmp(key, "getprogram", keyLength+1)) {
		//send current program
	}
	else if (!strncmp(key, "delay", keyLength+1)) {
		kilnRegulator.setState(KilnState::DELAYED);
		int delay = -1; //in s
		errCode = msgpack::readInt(stream, delay);
		if (errCode) { // not error code but success
			errCode = kilnRegulator.setWakeupDate(delay);
		} else {
			errCode = ErrorCode::BAD_REQUEST;
			goto readerror;
		}
	}
	sendAck(stream, msgId, key, errCode);
	kilnRegulator.updateState(); //update state as quick as possible for user expererience
	sendState(streamCRC, kilnRegulator);
	return true;
readerror:
	while (Serial.available()) Serial.read(); //clear input buffer
	sendAck(stream, msgId, key, errCode);
	return false;
}

void sendState(Stream &stream, KilnRegulator &kilnRegulator) {
	size_t mapSize = 9;

	uint32_t timestamp = now(); // get it first because it may send a time syncronisation request

	uint8_t state =  kilnRegulator.getState();
	uint8_t elementState =  kilnRegulator.getElementState();
	int8_t segment = kilnRegulator.getCurrentSegment();
	double temperature = kilnRegulator.getTemperature();

	msgpack::writeMapSize(stream, mapSize);

	msgpack::writeString(stream, "command");
	msgpack::writeString(stream, "status");

	msgpack::writeString5(stream, "s", 1); //"state"
	msgpack::writeIntU8(stream, state);

	msgpack::writeString5(stream, "eS", 2); //"elementState"
	msgpack::writeIntU8(stream, elementState);

	msgpack::writeString5(stream, "cS", 2); //"currentSegment"
	msgpack::writeInt8(stream, segment);

	msgpack::writeString5(stream, "t", 1); //"temperature"
	msgpack::writeFloat32(stream, temperature);

	msgpack::writeString5(stream, "o", 1); //"output"
	msgpack::writeFloat32(stream, kilnRegulator.output);

	msgpack::writeString5(stream, "sP", 2); //"setPoint"
	msgpack::writeFloat32(stream, kilnRegulator.setpoint);

	msgpack::writeString5(stream, "ts", 2); //"timestamp"
	msgpack::writeIntU32(stream, timestamp);
	
	msgpack::writeString5(stream, "d", 1); //"delay"
	if (state == KilnState::DELAYED){
		unsigned int secondesBeforeCooking = ((kilnRegulator.getWakeupDate() - now()));
		unsigned int minutesBeforeCooking = (unsigned int)(secondesBeforeCooking/60);
		msgpack::writeIntU32(stream, minutesBeforeCooking);
	}else{
		msgpack::writeIntU32(stream, 0);
	}
		
}


void setup() {
	Serial.begin(115200);
	while (!Serial) continue;

	kilnRegulator.setState(KilnState::LOADING);

	thermocouple.begin();

	thermocouple.setThermocoupleType(MAX31856_TCTYPE_S);

	delay(500); // wait for MAX chip to stabilize

	// Shut off embedded LED
	pinMode(2, OUTPUT);
	digitalWrite(2, LOW);

	watchdog.init();

	lcdMonitor.init();

	kilnRegulator.init();
	setSyncProvider(requestTime);
	setTime(1); // important to init it to one since lastTimesyncRequest is reset to 0
	kilnRegulator.updateState();
	sendState(streamCRC, kilnRegulator);
	samplingTimer.start(millis());
}

void loop() {

	if (Serial.available()) {
		receiveMessage(streamCRC, kilnRegulator);
	}

	samplingTimer.update(millis());
	if (samplingTimer.expired()) {
		kilnRegulator.updateState();
		sendState(streamCRC, kilnRegulator);
		samplingTimer.start(millis());
	}

	if (lastTimesyncRequest > 0 && lastTimesyncRequest + timeout < millis()) { // timed out
		strcpy(key, "timesync");
		sendAck(streamCRC, 0, key, ErrorCode::TIMEOUT);
		lastTimesyncRequest = 0;
		timeoutCounter++;
		if (timeoutCounter > 3) {
			// 3 timesync requests timed out, raspberry most likely not answering, do something…
		}
	}

	lcdMonitor.draw(kilnRegulator);

	watchdog.update();
	delay(1000);
}

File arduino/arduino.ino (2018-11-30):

#include <msgpack.hpp>

#include "KilnRegulator.h"

#define MAX_KEY_LENGTH 31

MAX6675 thermocouple(/*thermoCLK*/6, /*thermoCS*/5, /*thermoDO*/4);

KilnRegulator kilnRegulator(thermocouple);

char key[MAX_KEY_LENGTH+1] = "\0"; // buffer to store received map key

void sendAck(Stream &stream, char action[], int code) {
	size_t mapSize = 2;
	msgpack::writeMapSize(stream, mapSize);

	msgpack::writeString(stream, "ack");
	msgpack::writeString(stream, key);

	msgpack::writeString(stream, "code");
	msgpack::writeInt16(stream, code);
}

/*
 * Message format:
 * [ "command", param]
 */
bool receiveMessage(Stream &stream, KilnRegulator &kilnRegulator) {
	size_t arraySize;
	size_t keyLength;
	int errCode = 0;
	strcpy(key, "datatype");

	msgpack::DataType dataType;
	msgpack::getNextDataType(stream, dataType, true);
	sendAck(stream, key, dataType);
	strcpy(key, "request");

	errCode = msgpack::readArraySize(stream, arraySize);
	if (!errCode) { // not error code but success
		sendAck(stream, key, ErrorCode::BAD_REQUEST +10);
		goto readerror;
	}	

	if (arraySize < 0 || arraySize > 2) {
		sendAck(stream, key, ErrorCode::BAD_REQUEST +20);
		goto readerror;
	}

	errCode = msgpack::readString(stream, key, sizeof(key), keyLength);
	if (!errCode) { // not error code but success
		sendAck(stream, key, ErrorCode::BAD_REQUEST +30);
		goto readerror;
	}	

	if (!strncmp(key, "start", keyLength+1)) { //keyLength+1 because we want to compare null character as well
		errCode = kilnRegulator.start();
		//start cooking
		//read program
		sendAck(stream, key, errCode);
	} else if (!strncmp(key, "stop", keyLength+1)) {
		errCode = kilnRegulator.stop();
		//stop cooking
		sendAck(stream, key, errCode);
	} else if (!strncmp(key, "time", keyLength+1)) {
		//time synchronisation
	} else if (!strncmp(key, "setpoint", keyLength+1)) {
		if (arraySize < 2) {
			sendAck(stream, key, ErrorCode::BAD_REQUEST);
			goto readerror;
		}

		long setpoint = -1;
		msgpack::readInt(stream, setpoint);
		errCode = kilnRegulator.setSetpoint(setpoint);
		//set setpoint
		sendAck(stream, key, errCode);
	} else if (!strncmp(key, "getprogram", keyLength+1)) {
		//send current program
	}
	return true;
readerror:
	while (Serial.available()) Serial.read(); //clear input buffer
	return false;
}

void sendState(Stream &stream, KilnRegulator &kilnRegulator) {
	size_t mapSize = 5;

	int state =  kilnRegulator.getState();
	int elementState =  kilnRegulator.getElementState();
	int segment = kilnRegulator.getCurrentSegment();
	double temperature = kilnRegulator.getTemperature();
  
	msgpack::writeMapSize(stream, mapSize);

	msgpack::writeString(stream, "command");
	msgpack::writeString(stream, "status");

	msgpack::writeString(stream, "state");
	msgpack::writeInt16(stream, state);

	msgpack::writeString(stream, "elementState");
	msgpack::writeInt16(stream, elementState);

	msgpack::writeString(stream, "currentSegment");
	msgpack::writeInt16(stream, segment);

	msgpack::writeString(stream, "temperature");
	msgpack::writeFloat32(stream, temperature);
}


void setup() {
	Serial.begin(115200);
	while (!Serial) continue;
	delay(500); // wait for MAX chip to stabilize

	// Shut off embedded LED
	pinMode(13, OUTPUT);
	digitalWrite(13, LOW);
}

void loop() {
	if (Serial.available()) {
		receiveMessage(Serial, kilnRegulator);
	}
	kilnRegulator.updateState();
	sendState(Serial, kilnRegulator);
	delay(500);
}

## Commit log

2018-11-19 Display program list and buttons to launch a cooking
2018-11-20 Get temperature periodically + improve navigation (fixes + alerts)
2018-11-22 Fix back button listener thanks to navigation lifecycle + init program creation page
2018-11-27 Make a difference between units (temperature and time) for dev and for users
2018-11-30 Prototype REST API to get current temp from Arduino
2018-11-30 Cleaner Arduino project with Arduino Makefile
2018-11-30 Arduino README.md
2018-11-30 Add bin/www and remove bin/ from toplevel .gitignore…
2018-11-30 Send stop, start and setpoint commands to Arduino
2018-11-30 Arduino: Parse message and handle start/stop/setpoint commands
2018-11-30 Arduino regulation + submodules for arduino libraries
2018-11-30 NodeJS auto reconnect to Arduino on close/error
    [arduino.js]
2018-11-30 additional checks to recover from serial port error
    [arduino.js]
2018-11-30 Arduino: Compute and send CRC8 of message with acknowledgment
2018-11-30 Dockerized Arduino code deployment
2018-11-30 Arduino: remove datatype debugging
2018-11-30 Arduino: fix Dockerfile
2018-11-30 NodeJS: handle CRC and messageId Try to send stop automatically again in case of failure
2018-11-30 NodeJS: error logger and errors endpoint
    [arduino.js]
2018-11-30 Arduino: initialize windowStartTime rather than windowSize
2018-11-30 NodeJS stopCooking arduinoRepository → arduino
2018-11-30 Arduino: control pin 2 as well as pin 13, set pin low on stop
2018-11-30 Arduino: outputPin as parameter of KilnRegulator constructor
2018-11-30 Arduino: receive timestamp in seconds for Time library
2018-11-30 nodeJS send timestamp in seconds to arduino upon timestamp request
2018-11-30 Arduino: Check for timeout in timesync requests
2018-11-30 Arduino: regulate from segments
2018-11-30 NodeJS: output message buffer for Arduino
2018-11-30 Arduino: add Time library to Makefile
2018-11-30 NodeJS: start takes uuid and send program to arduino from programrepository
2018-11-30 Arduino: add RobTillaart/Arduino libraries for IEEE754tools.h
2018-11-30 arduino: receive and run program (still need some safetychecks
2018-11-30 Arduino: Add Arduino/libraries/IEEE754tools to Maefile
2018-11-30 Arduino: add Adafruit-MAX31855-library for MAX31855 thermocouple ADC
2018-11-30 Arduino: fix Makefile path
2018-11-30 NodeJS: deal with Mongo hell — reconstruct programs coming from database
2018-11-30 Arduino: handle min temp with negative slope
2018-11-30 Update raspberrypi/README.md, add some Raspberry config files and add Docker files for both arm/x86_64 deploymenet
2018-11-30 raspberry/README.md: docker-compose start arduino before server
2018-12-03 Fix merge… :(
    (cherry picked from commit 0965d2ffbddc28796d7070403680bd0eda5c5fd8)
2018-12-03 Arduino: MAX6675→MAX31855
2018-12-03 NodeJS: emit ack-<command> event when receiving ack from Arduino
2018-12-03 NodeJS: update current cooking state
2018-12-03 NodeJS: send current cooking state for GET /status/cooking
2018-12-03 NodeJS: persistant cookings + manually compute offset for timestamp (handles slight time desync between Arduino/Raspberry)
2018-12-04 RaspberryPi: conf/README.md watchdog configuration
2018-12-04 RaspberryPi: workaround for https://github.com/systemd/systemd/issues/5043
2018-12-04 RaspberryPi: fix watchdog config
2018-12-04 Arduino: watchdog with 8s timeout
2018-12-04 RaspberryPi: workaround MongoDB not cleaning lockfile on shutdown
2018-12-04 Arduino: add simple Timer
2018-12-04 Arduino: samplerate using timer for KilnRegulator
2018-12-05 Shorten Arduino status message to prevent buffer overrun (eg. send status then timesync)
    [KilnRegulator.cpp, KilnRegulator.h, main.cpp]
2018-12-05 Arduino: change elementState when heating/cooling
2018-12-05 NodeJS: fix getStatus with new arduinokilnregulator status
2018-12-05 Arduino: remove timestamp from ack errCode
2018-12-05 NodeJS: fix sample temperature in db
2018-12-05 Arduino: get timestamp before starting to send status since it may send a timesync request inbetween
2018-12-06 doc/LICENSES.md Raspberry Pi
2018-12-06 LICENSES.md Arduino framework
2018-12-06 Raspberry Pi: README.md init rpi3-mongodb3
2018-12-06 Arduino: README.md with instructions to set up Arduino IDE
2018-12-06 Add views for tracking (temperature and time stats) + Fix UI bugs (cursor for editing programs, header for table, page names) + Loading page with gif + Changing thermometer icon during cooking + Comp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
2018-12-06 Fix estimated temperature computation in cooking tracking
2018-12-07 NodeJS: compute relative timestamp and collect samples even in stopped state
2018-12-07 Implement reset command to switch from stopped to ready state
    [KilnRegulator.cpp, KilnRegulator.h, main.cpp]
2018-12-10 NodeJS: try to handle msgpack5 encoder errors
2018-12-10 Arduino: start working on LCD display
2018-12-11 RaspberryPi: Restart Mongo automatically
2018-12-11 RaspberryPi: configuration for NATed WiFi AP
2018-12-11 RaspberryPi: network configuration in README.md
2018-12-11 RaspberryPi: Add some scripts for auto configuration
2018-12-11 RaspberryPi: update README.md
2018-12-11 Program duplication feature + improve program storage + edit program with icon button + fix negative numbers in table
2018-12-14 NodeJS: don't start cooking if arduino is in error state
2018-12-14 DEVELOPERS.md: add some info about Raspberry Pi—Arduino communications
2018-12-14 Arduino: set segment count to 0 on reset
    [main.cpp]
2018-12-14 NodeJS: …
2018-12-14 Errors page in settings and on cooking launching in case of error
2018-12-14 Arduino: remove unused libraries
2018-12-14 Swagger: remove body from delete progams…
2018-12-14 Arduino: properly reset PID and use pin 2 for LED (13 conflicts with SCK
    [KilnRegulator.cpp]
2018-12-14 Arduino: LED ouptut pin 2
2018-12-14 Arduino: CS pin 7 for thermocouple
2019-01-03 change windows size, improve screen, change wiring and change pid params+ fix reset state
    [KilnRegulator.cpp, KilnRegulator.h, main.cpp]
2019-07-31 update timing aspects (sample every 10s, synchronize every 5 seconds)
2019-08-02 add hardware work
    [NodeMCU lolin Temperature relay lcd.fzz, Relay.fzz, fotocelda-inversor.fzz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]
2019-08-06 correct delayed cooking mobile side
    [main.cpp]
2019-08-07 fix bug for delayed cooking
    [KilnRegulator.cpp, KilnRegulator.h, main.cpp]
2019-08-09 implements full heat segments
2019-08-09 implements the full heat segments in the app
2019-08-13 hardware stuff
    [Relay.fzz, kilRegulator_controlerSchematic_v4.fzz, kilRegulator_controlerSchematic_v4_arduinoNano.fzz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]
2019-08-15 minor changes: put only 1 sample on 4 in the database, change default temp to 35, ensure adjustment is done if full is last segment
2019-08-18 correct the missing segment after an extension of a max segment
    [KilnRegulator.cpp]
2019-09-07 Update install_docker.sh
    add --no-install-recommends option to apt to avoid problems with afs dkms (see here: https://github.com/raspberrypi/linux/issues/3021)
2019-09-23 remove compile stuff
    [kilRegulator_controlerSchematic_v4_arduinoNano_pizero.fzz]
2019-09-29 add a loading screen on the arduino. Avoid connexion error when arduino is down
    [main.cpp]
2019-09-29 add conf files when used on Raspberry pizero W without docker
2019-09-30 add regulator pict
